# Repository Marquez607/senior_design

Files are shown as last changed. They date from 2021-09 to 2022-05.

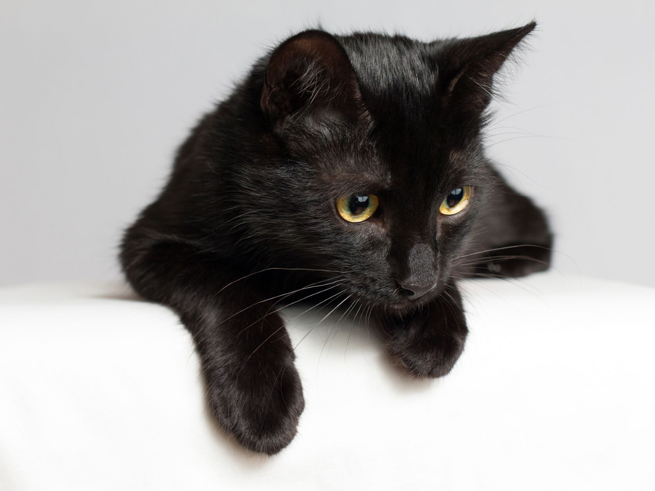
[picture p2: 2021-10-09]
Python/client_scripts/image_testing/test_cat.jpg

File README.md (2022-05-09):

# Wheelson IoT Drone Platform
Senior Design 2021 project by Marquez Jones and Daniel Olis \
Project consisted of making wifi connected robot platform that provided video streaming to end user on web application written with PyWebio. 

## MCU DETAILS 
### CC3235S <- base MCU 
* https://www.ti.com/product/CC3235S#design-development
### Launchpad :
* link: https://www.ti.com/tool/LAUNCHXL-CC3235S
### CC3235MODAS <- module that has antenna solution implemented
* link: https://www.ti.com/product/CC3235MODAS?keyMatch=&tisearch=search-everything&usecase=partmatches
### Launchpad :
* link: https://www.ti.com/tool/LAUNCHCC3235MOD

### NOTE: clean project before each build to make sure image file gets generated
* https://dev.ti.com/tirex/explore/node?node=AFiRjv8UYvIlGLFBWWEcQw__fc2e6sr__LATEST

### OUR BOARD
* may need to have a serial flash along side the MCU, steal the one from TI schematics
* Might only be necessary if we use the SysConfig ImageCreator 
* https://dev.ti.com/tirex/explore/node?node=AFiRjv8UYvIlGLFBWWEcQw__fc2e6sr__LATEST

<!-- ## Machine Learning 
Part of the project could be incorporating a camera to detect something. Right now it'd be 
cool if we could tell the drone to go to x,y gps location and look for trash. We can just 
get some trash dataset and train an support vector machine (or some other light weight ML model)

TinyML Guide (porting sklearn to c/++)
https://techcommunity.microsoft.com/t5/educator-developer-blog/using-tinyml-to-classify-audio/ba-p/2163436

Trash classification:
https://medium.com/geekculture/classifying-waste-images-with-machine-learning-14b249f11544#66db

Kaggle Waste Dataset:
https://www.kaggle.com/techsash/waste-classification-data -->

## WIFI CONNECTIVITY
For sanity's sake, the system will get deployed on using a LAN router we have control over
I'll be using a static IP address for the robot/drone that I'll configure using the router. 
Without a static IP, I'd probably have to seput some kind of website or blah blah blah 

## USER INTERFACE
We can quickly make a webapp using pywebio:
https://pywebio.readthedocs.io/en/latest/search.html?q=image&check_keywords=yes&area=default#

This can be hosted on the same "server" as the wifi drone controller which will just be a computer on our LAN network.
This way, it can be used on both PC and mobile without having to compile multiple applications and should be sufficient 
for the scope of this project. 

Jank way to implement video streaming in pywebio:
https://github.com/pywebio/PyWebIO/issues/107

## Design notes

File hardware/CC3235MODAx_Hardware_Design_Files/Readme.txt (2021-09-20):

CC3235MODAx Hardware Design Files v1.00.00
Texas Instruments, Inc.

********************************************************************************
Welcome to the CC3235MODAx Dual-Band Wi-Fi Wireless MCU Module!
********************************************************************************

In this package, you will find hardware design files that can help you quickly
get started on developing your own project.

Available in the 'Hardware' folder are the complete board schematic and layout,
bill of material and Gerber files. This board was designed using Altium.

You can also a web link in the 'Documentation' folder pointing to
the Product Page.

For more resources, be sure to visit www.ti.com/product/cc3235moda

********************************************************************************
Revision History
********************************************************************************
Ver 1.00.00 - October 2, 2019
- Initial Release of Rev A

********************************************************************************
Project File Listing
********************************************************************************
|--Documentation                      : Folder containing links to more resources
|--Hardware                           : Folder containing hardware design files,
                                        bill of material and gerber files
|--Readme.txt                         : This file

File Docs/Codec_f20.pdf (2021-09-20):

# GND Tip

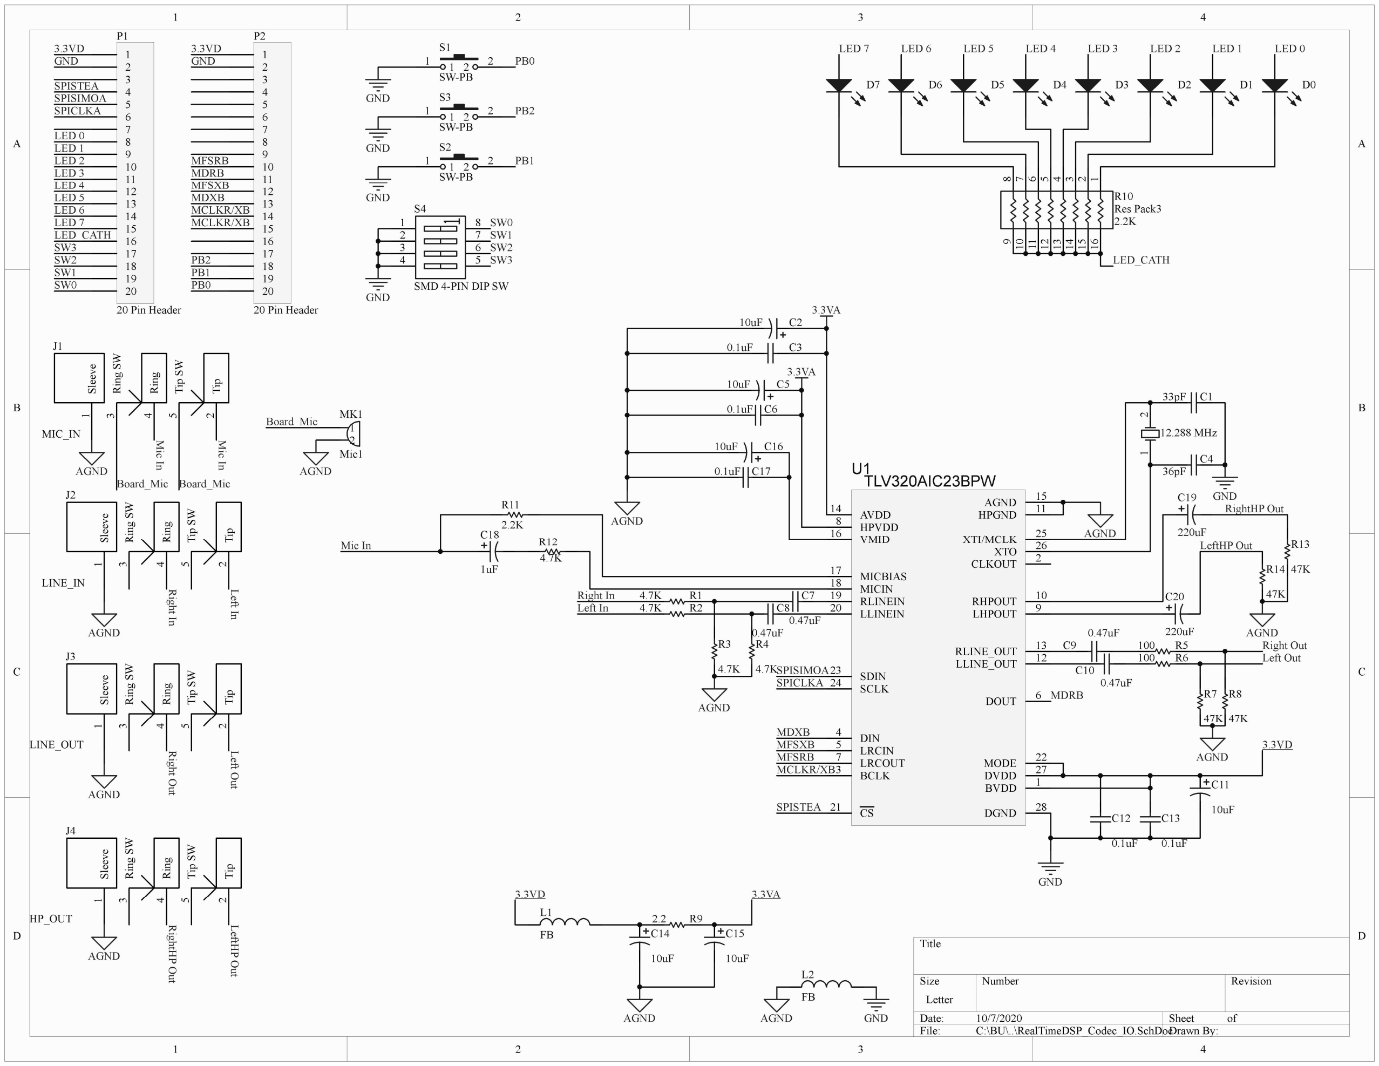
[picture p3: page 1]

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
Title

Size | Number | | Revision
Letter
Date: | 10/7/2020 | Sheet | of
File: | C:\BU\..\RealTimeDSP_Codec_IO.SchDocDrawn By:
0.1uF | C3
10uF | C2

0.1uF C6

10uF C5

AGND

0.47uF

C7

0.47uF

C8

4.7K | R1
4.7K | R2

4.7K

R4

4.7K

R3

Right In
Left In

AGND

33pF C1

36pF

C4 ¹ ² 12.288 MHz

GND

AGND

0.47uF

C10

0.47uF
C9

47K

R7

47K

R8

100 R5
100 R6

Right Out
Left Out

AGND

0.1uF

C12

0.1uF

C13

10uF

C11

GND

3.3VD

L1

FB

3.3VD

10uF

C14

10uF

C15

### 2.2 R9

3.3VA

AGND | AGND | GND

L2

FB Tip

### 2 Ring

### 4 Sleeve 1 Ring SW 3 Tip SW

5

J2

LINE_IN | Tip

### 2 Ring

### 4 Sleeve 1 Ring SW 3 Tip SW

5

J3

LINE_OUT

AGND | Right In | Left In
AGND | Right Out | Left Out

SPICLKA

MDXB
MFSXB
MFSRB

SPISTEA

MDRB

LHPOUT 9

LRCOUT 7

RHPOUT | 10
DOUT | 6
XTO | 26
RLINE_OUT | 13
LLINE_OUT | 12
CLKOUT | 2
MICBIAS 17
HPGND | 11
DGND | 28
AGND | 15

SDIN 23

DIN 4

CS 21

MODE 22

VMID 16

MICIN 18

LRCIN 5

XTI/MCLK 25

RLINEIN 19
LLINEIN 20

SCLK 24

HPVDD 8

DVDD | 27
BVDD | 1

AVDD 14

BCLK 3

U1

## TLV320AIC23BPW

SPISIMOA

MCLKR/XB

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
### 20 Pin Header

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
SMD 4-PIN DIP SW
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
### 20 Pin Header Tip

### 2 Ring

### 4 Sleeve 1 Ring SW 3 Tip SW

5

J1

MIC_IN

AGND

10uF C16

0.1uF C17

3.3VA

3.3VA Mic In | Mic In

2.2K

R11

Mic In
4.7K

R12

1

1
2

2

S1

SW-PB

1

1
2

2

S2

SW-PB

GND

PB2 1

1
2

2

S3

SW-PB

D7 | D6 | D5 | D4 | D3 | D2 | D1 | D0 8

7

6

5

4

3

2

1 101112131415169

2.2K

R10
Res Pack3
LED 7 | LED 6 | LED 5 | LED 4 | LED 3 | LED 2 | LED 1 | LED 0

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
220uF

C19

220uF

C20

47K

R13

47K

R14

AGND

LED_CATH

3.3VD

### 2 Ring

### 4 Sleeve 1 Ring SW 3 Tip SW

5

J4

HP_OUT

1
2

MK1

Mic1

Board_Mic

AGND

# Board_Mic Board_Mic RightHP Out LeftHP Out

RightHP Out

LeftHP Out

AGND

LED 0
LED 1
LED 2
LED 3
LED 4
LED 5
LED 6
LED 7

MFSRB
MDRB
MFSXB
MDXB
MCLKR/XB
MCLKR/XB

3.3VD
GND

LED_CATH

SPISTEA
SPISIMOA
SPICLKA

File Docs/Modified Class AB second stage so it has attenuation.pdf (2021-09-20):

Modified Class AB second stage so it has attenuation. You need to do this if your signal is on the level of 1V or more going into the Class AB power amplifier. You can tweak the values to get the Class AB response louder.

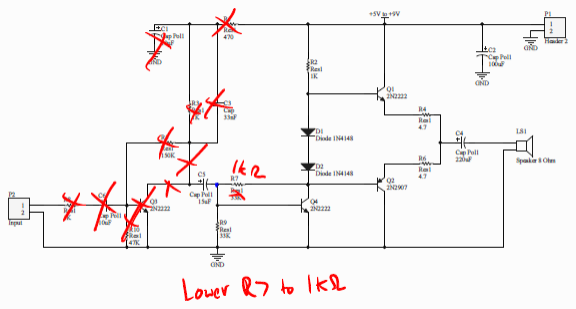
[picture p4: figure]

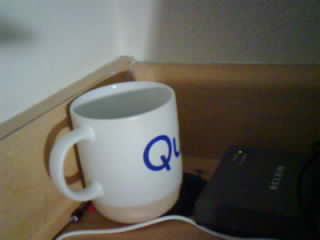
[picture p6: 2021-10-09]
Python/client_scripts/good_images/snap_5.jpg

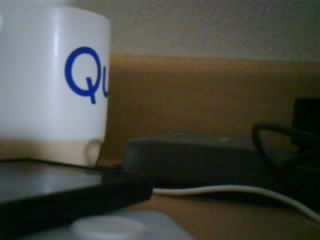
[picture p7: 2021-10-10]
Python/client_scripts/rx_images/snap_3.jpg

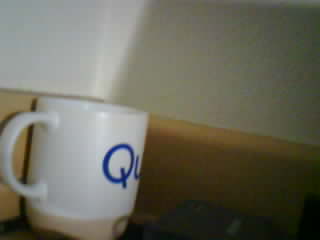
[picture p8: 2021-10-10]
Python/client_scripts/rx_images/snap_86.jpg

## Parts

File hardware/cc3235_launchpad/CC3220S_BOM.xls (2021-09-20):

Filename: | WCS002A_CC3220S_BOM.xls
Variant: | 002
Generated: | 12/6/2016 1:31:22 PM
 |  | CC3220S-LAUNCHXL
Designator | Quantity | Value | Description | PackageReference | PartNumber | Manufacturer | Alternate PartNumber | Alternate Manufacturer
!PCB1 | 1 |  | Printed Circuit Board |  | WCS002 | Any | - | -
C1, C4, C5, C14, C17, C24, C25, C28, C32, C33, C36, C37, C38, C43, C44, C46, C47, C57, C58, C59 | 20 | 0.1uF | CAP, CERM, 0.1 µF, 10 V, +/- 10%, X5R, 0402 | 0402 | C1005X5R1A104K050BA | TDK
C2, C3, C7, C8, C9, C15, C21, C53, C54, C55, C56 | 11 | 0.01uF | CAP, CERM, 0.01 µF, 16 V, +/- 10%, X7R, 0402 | 0402 | C1005X7R1C103K | TDK
C6, C13 | 2 | 22pF | CAP, CERM, 22 pF, 50 V, +/- 1%, C0G/NP0, 0402 | 0402 | GRM1555C1H220FA01D | MuRata
C10, C11, C19 | 3 | 0.1uF | CAP, CERM, 0.1 µF, 25 V, +/- 10%, X5R, 0603 | 0603 | 06033D104KAT2A | AVX
C12, C16, C20, C22, C23 | 5 | 1uF | CAP, CERM, 1 µF, 16 V, +/- 10%, X5R, 0402 | 0402 | C1005X5R1C105K050BC | TDK
C18 | 1 | 2.2uF | CAP, CERM, 2.2 µF, 16 V, +/- 10%, X5R, 0402 | 0402 | C1005X5R1C225K050BC | TDK
C26, C48, C49 | 3 | 10pF | CAP, CERM, 10 pF, 50 V, +/- 5%, C0G/NP0, 0402 | 0402 | GRM1555C1H100JA01D | MuRata
C27 | 1 | 1uF | CAP, CERM, 1 µF, 10 V, +/- 10%, X5R, 0402 | 0402 | GRM155R61A105KE15D | MuRata
C29, C30, C31 | 3 | 4.7uF | CAP, CERM, 4.7 µF, 6.3 V, +/- 20%, X5R, 0402 | 0402 | C1005X5R0J475M050BC | TDK
C34 | 1 | 0.5pF | CAP, CERM, 0.5 pF, 50 V, +/- 10%, C0G/NP0, 0402 | 0402 | GJM1555C1HR50BB01J | MuRata
C35, C42, C45 | 3 | 10uF | CAP, CERM, 10 µF, 6.3 V, +/- 20%, X5R, 0603 | 0603 | GRM188R60J106ME47D | MuRata
C39, C40 | 2 | 22uF | CAP, CERM, 22 µF, 4 V, +/- 20%, X5R, 0603 | 0603 | C1608X5R0G226M080AA | TDK
C41 | 1 | 1uF | CAP, CERM, 1 µF, 10 V, +/- 10%, X5R, 0402 | 0402 | C1005X5R1A105K050BB | TDK
C50, C51 | 2 | 6.2pF | CAP, CERM, 6.2 pF, 50 V, +/- 5%, C0G/NP0, 0402 | 0402 | GRM1555C1H6R2CA01D | MuRata
C52 | 1 | 0.01uF | CAP, CERM, 0.01 µF, 10 V, +/- 10%, X5R, 0402 | 0402 | GRM155R61A103KA01D | MuRata
C60, C62 | 2 | 10uF | CAP, CERM, 10 µF, 10 V, +/- 10%, X5R, 0805 | 0805 | GRM21BR61A106KE19L | MuRata
C61 | 1 | 22uF | CAP, CERM, 22 µF, 16 V, +/- 10%, X5R, 0805 | 0805 | C2012X5R1C226K125AC | TDK
C63, C64 | 2 | 100uF | CAP, CERM, 100 µF, 6.3 V, +/- 20%, X5R, 1206 | 1206 | GRM31CR60J107ME39L | MuRata
D1, D8 | 2 | Green | LED, Green, SMD | LED, GREEN, 0603 | SML-LX0603GW-TR | Lumex
D2, D6, D7, D10 | 4 | Red | LED, Red, SMD | LED, 1.6x.8x.8mm | SML-311UTT86 | Rohm
D3, D9 | 2 | Yellow | LED, Yellow, SMD | LED_0603 | 150060YS75000 | Wurth Elektronik eiSos
D4, D5 | 2 | 45V | Diode, Schottky, 45 V, 0.03 A, 0603 Diode | 0603 Diode | CD0603-B00340 | Bourns
E1 | 1 |  | ANT BLUETOOTH W-LAN ZIGBEE WIMAX, SMD | 3.2x1.6mm | AH316M245001-T | Taiyo Yuden
FL1 | 1 | 1.02 dB | Multilayer Chip Band Pass Filter For 2.4GHz W-LAN/Bluetooth, SMD | 2x1.25mm | DEA202450BT-1294C1-H | TDK
J1 | 1 |  | Connector, Receptacle, Micro-USB Type B, R/A, Bottom Mount SMT | Micro USB receptacle | 105017-0001 | Molex
J3 | 1 |  | Header, 2.54 mm, 5x2, Gold, TH | Header, 2.54mm, 5x2, TH | 61301021121 | Wurth Elektronik
J4, J8 | 2 |  | Header, 1.27 mm, 5x2, Gold, TH | Header, 1.27 mm, 5x2, TH | FTSH-105-01-F-D-K | Samtec
J5, J6, J22, J23 | 4 |  | Header, 2.54 mm, 3x1, Gold, TH | Header, 2.54mm, 3x1, TH | 61300311121 | Wurth Elektronik
J7 | 1 |  | Header, 1.27mm, 7x2, Gold, SMT | Header, 1.27mm, 7x2, SMT | FTSH-107-01-F-DV | Samtec
J9, J15, J16, J17, J18, J19, J20, J21, J24 | 9 |  | Header, 2.54 mm, 2x1, Gold, TH | Header, 2.54mm, 2x1, TH | 61300211121 | Wurth Elektronik
J10 | 1 |  | Connector, Ultra-Mini Coaxial, SMD | Ultra small CO-AX SMD | U.FL-R-SMT-1 | Hirose Electric Co. Ltd.
J11 | 1 |  | Coaxial Connectors with Switch, 50 Ohm, SMD | Coaxial Connector with Switch | MM8030-2610RJ3 | MuRata
J13 | 1 |  | Header, 2.54mm, 3x2, Gold, TH | Header, 2.54mm, 3x2, TH | 61300621121 | Wurth Elektronik
L1, L2 | 2 | 10 ohm | Ferrite Bead, 10 ohm @ 100 MHz, 1 A, 0402 | 0402 | BLM15AG100SN1D | MuRata
L3 | 1 | 3.3nH | Inductor, Multilayer, Air Core, 3.3 nH, 0.3 A, 0.17 ohm, SMD | 0402 polarized | LQG15HS3N3S02D | MuRata
L4, L6 | 2 | 2.2uH | Inductor, Multilayer, Ferrite, 2.2 µH, 1.3 A, 0.08 ohm, SMD | SMD, Body 2.5x2mm, Height 1.2mm | LQM2HPN2R2MG0L | MuRata
L5 | 1 | 1uH | Inductor, Multilayer, Ferrite, 1 µH, 1.6 A, 0.055 ohm, SMD | SMD, Body 2.5x2mm, Height 1.2mm | LQM2HPN1R0MG0L | MuRata
L8 | 1 | 2.2uH | Inductor, Wirewound, 2.2 µH, 1 A, 0.143 ohm, SMD | 0805_140 | BRC2012T2R2MD | Taiyo Yuden
LBL1 | 1 |  | Thermal Transfer Printable Labels, 0.650" W x 0.200" H - 10,000 per roll | PCB Label 0.650"H x 0.200"W | THT-14-423-10 | Brady | - | -
P1, P2, P3, P4 | 4 |  | Connector, Receptacle, 100mil, 10x1, Gold plated, TH | 10x1 Receptacle | SSW-110-23-F-S | Samtec
Q1, Q4, Q6, Q7 | 4 | 50V | MOSFET, N-CH, 50 V, 0.22 A, SOT-23 | SOT-23 | BSS138 | Fairchild Semiconductor |  | None
Q2 | 1 | -50V | MOSFET, P-CH, -50 V, -0.13 A, AEC-Q101, SOT-363 | SOT-363 | BSS84DW-7-F | Diodes Inc. |  | None
Q3, Q5 | 2 | -30V | MOSFET, P-CH, -30 V, -1.5 A, SSOT-3 | SSOT-3 | FDN358P | Fairchild Semiconductor |  | None
R1, R2, R3, R4, R5, R6, R8, R27, R31 | 9 | 33.0 | RES, 33.0, 1%, 0.1 W, 0402 | 0402 | ERJ-2RKF33R0X | Panasonic
R7, R9, R10, R11, R25, R29, R30, R32, R137, R138, R139, R144 | 12 | 1.0k | RES, 1.0 k, 5%, 0.063 W, 0402 | 0402 | CRCW04021K00JNED | Vishay-Dale
R12, R39, R40, R43, R44, R45, R46, R60, R62, R64, R67, R68, R70, R71, R72, R74, R75, R76, R78, R80, R81, R82, R83, R84, R85, R86, R87, R88, R89, R90, R91, R92, R116, R117, R121, R123, R126, R128, R129, R130, R132, R133, R134, R135, R154 | 45 | 0 | RES, 0, 5%, 0.063 W, 0402 | 0402 | ERJ-2GE0R00X | Panasonic
R13 | 1 | 100 | RES, 100, 5%, 0.063 W, 0402 | 0402 | CRCW0402100RJNED | Vishay-Dale
R14 | 1 | 100k | RES, 100 k, 5%, 0.1 W, 0603 | 0603 | CRCW0603100KJNEA | Vishay-Dale
R15 | 1 | 330k | RES, 330 k, 5%, 0.063 W, 0402 | 0402 | CRCW0402330KJNED | Vishay-Dale
R16 | 1 | 220k | RES, 220 k, 5%, 0.063 W, 0402 | 0402 | CRCW0402220KJNED | Vishay-Dale
R17, R26, R41, R48, R49, R50, R136, R146, R151, R152, R153 | 11 | 100k | RES, 100 k, 5%, 0.063 W, 0402 | 0402 | CRCW0402100KJNED | Vishay-Dale
R51 | 1 | 2.7k | RES, 2.7 k, 5%, 0.063 W, 0402 | 402 | CRCW04022K70JNED | Vishay-Dale
R18, R19 | 2 | 220 | RES, 220, 5%, 0.1 W, 0603 | 0603 | CRCW0603220RJNEA | Vishay-Dale
R20, R35, R53, R141, R142 | 5 | 10k | RES, 10 k, 5%, 0.063 W, 0402 | 0402 | CRCW040210K0JNED | Vishay-Dale
R21 | 1 | 100 | RES, 100, 1%, 0.1 W, 0402 | 0402 | ERJ-2RKF1000X | Panasonic
R22 | 1 | 100 | RES, 100, 1%, 0.063 W, 0402 | 0402 | CRCW0402100RFKED | Vishay-Dale
R23 | 1 | 4.87k | RES, 4.87 k, 1%, 0.1 W, 0603 | 0603 | CRCW06034K87FKEA | Vishay-Dale
R24, R143, R145, R147, R148, R149 | 6 | 270 | RES, 270, 5%, 0.1 W, 0603 | 0603 | CRCW0603270RJNEA | Vishay-Dale
R28 | 1 | 51 | RES, 51, 5%, 0.063 W, 0402 | 0402 | CRCW040251R0JNED | Vishay-Dale
R33, R34 | 2 | 33 | RES, 33, 5%, 0.1 W, 0603 | 0603 | CRCW060333R0JNEA | Vishay-Dale
R36, R57 | 2 | 0 | RES, 0, 5%, 0.1 W, 0603 | 0603 | ERJ-3GEY0R00V | Panasonic
R47 | 1 | 270 | RES, 270, 5%, 0.063 W, 0402 | 0402 | CRCW0402270RJNED | Vishay-Dale
R52 | 1 | 2.2k | RES, 2.2 k, 5%, 0.063 W, 0402 | 0402 | CRCW04022K20JNED | Vishay-Dale
R102, R105, R110, R111 | 4 | 470 | RES, 470, 1%, 0.1 W, 0402 | 0402 | ERJ-2RKF4700X | Panasonic
R103, R104, R112, R113 | 4 | 576k | RES, 576 k, 1%, 0.063 W, 0402 | 0402 | CRCW0402576KFKED | Vishay-Dale
R106, R107, R114, R115 | 4 | 422k | RES, 422 k, 1%, 0.063 W, 0402 | 0402 | CRCW0402422KFKED | Vishay-Dale
R118, R119 | 2 | 3.3k | RES, 3.3 k, 5%, 0.063 W, 0402 | 0402 | CRCW04023K30JNED | Vishay-Dale
R140 | 1 | 100k | RES, 100 k, 1%, 0.1 W, 0402 | 0402 | ERJ-2RKF1003X | Panasonic
SW1, SW2, SW3 | 3 |  | Switch, SPST-NO, Off-Mom, 1 Pos, 0.05A, 12VDC, TH | 7.3x5.9mm | MJTP1117 | APEM
SW4 | 1 |  | Switch, Tactile, SPST-NO, SMT | Switch, 6.1x1.8x4.6 mm | EVQ-PSD02K | Panasonic
TP2 | 1 | SMT | Test Point, Miniature, SMT | Testpoint_Keystone_Miniature | 5015 | Keystone
U1 | 1 |  | Tiva C Series Microcontroller, PDT0128A | PDT0128A | TM4C1294NCPDTI3R | Texas Instruments | TM4C1294NCPDTI3 | Texas Instruments
U2 | 1 |  | ESD Solution for High-Speed Differential Interface, 4 Channels, -40 to +85 degC,10-pin SON (DQA), Green (RoHS & no Sb/Br) | DQA0010A | TPD4S010DQAR | Texas Instruments | Equivalent | Texas Instruments
U3, U4, U6 | 3 |  | Single-Bit Dual-Supply Bus Transceiver With Configurable Voltage Translation and 3-State Outputs, DCK0006A | DCK0006A | SN74LVC1T45DCKR | Texas Instruments | SN74LVC1T45DCKT | Texas Instruments
U5 | 1 |  | Precision Micropower Shunt Voltage Reference, 0.2% accuracy, 2.5 V, 15 ppm / degC, 15 mA, -40 to 85 degC, 3-pin SOT-23 (DBZ), Green (RoHS & no Sb/Br) | DBZ0003A | LM4040B25IDBZR | Texas Instruments | Equivalent | Texas Instruments
U7 | 1 |  | SimpleLink Wi-Fi and Internet-of-Things Solution, a Single-Chip Wireless MCU, RGK0064B (VQFN-64) | RGK0064B | CC3220SM2ARGKR | Texas Instruments | CC3220SM2ARGKT | Texas Instruments
U8 | 1 |  | ULTRA LOW POWER, 32M-BIT [x 1/x 2/x 4] CMOS MXSMIO(SERIAL MULTI I/O) FLASH MEMORY, SOP-8 | 8-SOP | MX25R3235FM1IL0 | Macronix International Co., LTD
U9 | 1 |  | Low Cost, Low Power, Rail-to-Rail Operational Amplifier MicroAmplifier(TM) Series, 2.7 to 5.5 V, -55 to 125 degC, 14-pin SOP (PW0014A), Green (RoHS & no Sb/Br) | PW0014A | OPA4342EA/250 | Texas Instruments | Equivalent | None
U10 | 1 |  | Infrared Thermopile Sensor in Chip-Scale Package, YZF0008AEAE | YZF0008AEAE | TMP006AIYZF | Texas Instruments |  | Texas Instruments
U11 | 1 |  | Digital, triaxial acceleration sensor, 12LGA | LGA, 12-Leads, Body 2x2mm, Pitch 0.5mm | BMA222E | Bosch Solar Energy
U12 | 1 |  | Buck Step Down Regulator with 3 to 17 V Input and 3.3 V Output, -40 to 85 degC, 8-Pin WSON (DSG), Green (RoHS & no Sb/Br) | DSG0008A | TPS62162DSGR | Texas Instruments | Equivalent | Texas Instruments
Y1 | 1 |  | Crystal, 16 MHz, 18 pF, SMD | ABM3 | ABM3-16.000MHZ-D2Y-T | Abracon Corportation
Y2 | 1 |  | CRYSTAL, 32.768KHZ, 9PF, SMD | 3.2x0.9x1.5mm | ABS07-32.768KHZ-9-T | Abracon Corportation
Y3 | 1 |  | Crystal, 40MHz, 8pF, SMD | 2.5x2mm | Q24FA20H0039600 | Epson
FID1, FID2, FID3, FID4, FID5, FID6 | 0 |  | Fiducial mark. There is nothing to buy or mount. | Fiducial | N/A | N/A
J14 | 0 |  | Header, 2.54 mm, 2x1, Gold, TH | Header, 2.54mm, 2x1, TH | 61300211121 | Wurth Elektronik
L7 | 0 | 10uH | Inductor, Wirewound, Ceramic, 10 µH, 0.48 A, 0.36 ohm, SMD | 2.5x1.8x1.8mm | CBC2518T100M | Taiyo Yuden
R37, R38, R42, R54, R55, R58, R59, R61, R63, R65, R66, R69, R73, R77, R79, R93, R94, R95, R96, R97, R98, R99, R100, R101, R108, R109, R120, R122, R124, R127, R131 | 0 | 0 | RES, 0, 5%, 0.063 W, 0402 | 0402 | ERJ-2GE0R00X | Panasonic
R56, R150 | 0 | 0 | RES, 0, 5%, 0.1 W, 0603 | 0603 | ERJ-3GEY0R00V | Panasonic
R125 | 0 | 0 | RES, 0, 5%, 0.125 W, 0805 | 0805 | ERJ-6GEY0R00V | Panasonic
 |  | Notes:
 |  | Unless otherwise noted in the Alternate PartNumber and/or Alternate Manufacturer columns, all parts may be substituted with equivalents.

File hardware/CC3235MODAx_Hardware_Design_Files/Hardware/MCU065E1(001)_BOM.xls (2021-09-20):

Filename: | #VALUE!
Variant: | 001
Generated: | 10/2/2019 2:32:45 PM
 |  | LAUNCHCC3235MODAS
Designator | Quantity | Value | Description | PackageReference | PartNumber | Manufacturer | Alternate PartNumber | Alternate Manufacturer
!PCB1 | 1 |  | Printed Circuit Board |  | MCU065 | Any
C1 | 1 | 0.1uF | CAP, CERM, 0.1 uF, 10 V,+/- 10%, X5R, 0402 | 0402 | LMK105BJ104KV-F | Taiyo Yuden
C2, C5, C6, C7, C12, C14 | 6 | 0.01uF | CAP, CERM, 0.01 µF, 16 V,+/- 10%, X7R, 0402 | 0402 | CL05B103KO5NNNC | Samsung Electro-Mechanics
C3, C13, C15, C18 | 4 | 1uF | CAP, CERM, 1 uF, 16 V, +/- 10%, X5R, 0402 | 0402 | EMK105BJ105KVHF | Taiyo Yuden
C4, C11 | 2 | 22pF | CAP, CERM, 22 pF, 50 V,+/- 5%, C0G/NP0, 0402 | 0402 | CL05C220JB5NNNC | Walsin
C8, C9, C10, C17 | 4 | 0.1uF | CAP, CERM, 0.1 uF, 25 V, +/- 10%, X5R, 0603 | 0603 | 06033D104KAT2A | AVX
C16 | 1 | 2.2uF | CAP, CERM, 2.2 uF, 16 V, +/- 10%, X5R, 0402 | 0402 | C1005X5R1C225K050BC | TDK
C19, C20, C22, C23, C29, C30, C31, C32, C33, C34, C40, C41, C42 | 13 | 0.1uF | CAP, CERM, 0.1 uF, 10 V, +/- 10%, X5R, 0402 | 0402 | GRM155R61A104KA01D | MuRata
C21, C36, C37, C38, C39 | 5 | 0.01uF | CAP, CERM, 0.01 uF, 16 V, +/- 10%, X7R, 0402 | 0402 | GRM155R71C103KA01D | MuRata
C24, C26 | 2 | 10uF | CAP, CERM, 10 uF, 10 V, +/- 10%, X5R, 0805 | 0805 | GRM21BR61A106KE19L | MuRata | CL21A106KPFNNNE | SAMSUNG
C25 | 1 | 22uF | CAP, CERM, 22 uF, 16 V, +/- 10%, X5R, 0805 | 0805 | C2012X5R1C226K125AC | TDK | ---- | ----
C27, C28 | 2 | 100uF | CAP, CERM, 100 uF, 6.3 V, +/- 20%, X5R, 1206 | 1206 | GRM31CR60J107ME39L | MuRata | CL31A107MQHNNNE | SAMSUNG
C35 | 1 | 0.01uF | CAP, CERM, 0.01 uF, 10 V, +/- 10%, X5R, 0402 | 0402 | GRM155R61A103KA01D | MuRata
CC1 | 1 |  | SimpleLink Wi-Fi and Internet-of-Things Module Solution, a Single-Chip Wireless MCU, MOB0063A (SIP MODULE-63) | MON0063A | CC3235MODASM2MONR | Texas Instruments |  | Texas Instruments
D1 | 1 | Green | LED, Green, SMD | LED, GREEN, 0603 | SML-LX0603GW-TR | Lumex
D2 | 1 | Red | LED, Red, SMD | SMD, 2-Leads, Body 1.6x0.8mm | 19-217/R6C-AL1M2VY/3T | Everlight
D3 | 1 | Yellow | LED, Yellow, SMD | LED_0603 | 150060YS75000 | Wurth Elektronik | 19-217/G7C-AN1P2/3T | Everlight
D4, D8 | 2 | Red | LED, Red, SMD | LED, 1.6x.8x.8mm | SML-311UTT86 | Rohm | 19-217/R6C-AL1M2VY/3T | Everlight
D5, D6 | 2 | 45V | Diode, Schottky, 45 V, 0.03 A, SOD-523F | SOD-523F | CDBU00340 | Comchip Technology
D7 | 1 | RGB | LED, RGB, TH | 1.6x1.6mm | 19-337/R6GHBHC-A01/2T | Everlight
H1, H2, H3, H4 | 4 |  | Spacer Support, Nylon 66 | Spacer Nylon Support | MAE-10 | Kang Yang
J1 | 1 |  | Receptacle, USB 2.0, Micro B, 5 Position, R/A, SMT | Receptacle, USB 2.0, Micro B, 5 Pos, 0.65mm Pitch, R/A, SMT | 1051640001 | Molex
J2, J6 | 2 |  | Header, 1.27 mm, 5x2, Gold, TH | Header, 1.27 mm, 5x2, TH | FTSH-105-01-F-D-K | Samtec | ---- | ----
J3 | 1 |  | Header, 1.27mm, 7x2, Gold, SMT | Header, 1.27mm, 7x2, SMT | FTSH-107-01-F-DV | Samtec | ---- | ----
J5 | 1 |  | Header, 2.54 mm, 5x2, Gold, TH | Header, 2.54mm, 5x2, TH | 61301021121 | Wurth Elektronik
J7, J8, J9, J10, J21, J22, J23, J24, J25 | 9 |  | Header, 2.54 mm, 2x1, Gold, TH | Header, 2.54mm, 2x1, TH | 61300211121 | Wurth Elektronik
J11, J12, J16 | 3 |  | Header, 2.54 mm, 3x1, Gold, TH | Header, 2.54mm, 3x1, TH | 61300311121 | Wurth Elektronik
J13 | 1 |  | Header, 2.54mm, 2x1, TH | Header, 2.54mm, 2x1, TH | 961102-6404-AR | 3M
J18 | 1 |  | Header, 2.54mm, 3x2, Gold, TH | Header, 2.54mm, 3x2, TH | 61300621121 | Wurth Elektronik
J19, J20 | 2 |  | Header, 100mil, 3x1, Tin, TH | Header, 3 PIN, 100mil, Tin | PEC03SAAN | Sullins Connector Solutions
L1, L2 | 2 | 10 ohm | Ferrite Bead, 10 ohm @ 100 MHz, 1 A, 0402 | 0402 | BLM15AG100SN1D | MuRata
L3 | 1 | 2.2uH | Inductor, Wirewound, 2.2 uH, 1 A, 0.143 ohm, SMD | 0805 | BRC2012T2R2MD | Taiyo Yuden | ---- | ----
LBL1 | 1 |  |  | PCB Label 0.650 x 0.200 inch | THT-14-423-10 | Brady
P1, P2 | 2 |  | Receptacle, 2.54mm, 10x2, Tin, TH | 10x2 Receptacle | SSQ-110-03-T-D | Samtec | CRD-081413-A-G | Major League Electronics
Q1, Q5, Q6, Q7 | 4 | 50V | MOSFET, N-CH, 50 V, 0.22 A, SOT-23 | SOT-23 | BSS138 | Fairchild Semiconductor |  | None
Q3 | 1 | -50V | MOSFET, 2-CH, P-CH, -50 V, -0.13 A, AEC-Q101, SOT-363 | SOT-363 | BSS84DW-7-F | Diodes Inc. |  | None
Q4 | 1 | -30V | MOSFET, P-CH, -30 V, -1.5 A, SSOT-3 | SSOT-3 | FDN358P | Fairchild Semiconductor |  | None
R1, R13, R16, R17, R18, R19, R20, R26, R148, R149, R154 | 11 | 1.0k | RES, 1.0 k, 5%, 0.063 W, AEC-Q200 Grade 0, 0402 | 0402 | CRCW04021K00JNED | Vishay-Dale
R2, R4, R6, R7, R8, R9, R10, R34, R37 | 9 | 33.0 | RES, 33.0, 1%, 0.1 W, 0402 | 0402 | ERJ-2RKF33R0X | Panasonic
R3, R45, R46, R104, R124, R125, R128, R130, R131, R135, R136, R137, R138, R140, R141 | 15 | 0 | RES, 0, 5%, 0.1 W, AEC-Q200 Grade 0, 0402 | 0402 | ERJ-2GE0R00X | Panasonic
R5 | 1 | 100 | RES, 100, 5%, 0.063 W, AEC-Q200 Grade 0, 0402 | 0402 | CRCW0402100RJNED | Vishay-Dale
R11 | 1 | 330k | RES, 330 k, 5%, 0.063 W, AEC-Q200 Grade 0, 0402 | 0402 | CRCW0402330KJNED | Vishay-Dale
R12 | 1 | 220k | RES, 220 k, 5%, 0.063 W, AEC-Q200 Grade 0, 0402 | 0402 | CRCW0402220KJNED | Vishay-Dale
R14, R15 | 2 | 220 | RES, 220, 5%, 0.1 W, AEC-Q200 Grade 0, 0603 | 0603 | CRCW0603220RJNEA | Vishay-Dale
R21, R22 | 2 | 33 | RES, 33, 5%, 0.1 W, AEC-Q200 Grade 0, 0603 | 0603 | CRCW060333R0JNEA | Vishay-Dale | RC0603JR-0733RL | YAGEO
R23 | 1 | 51 | RES, 51, 5%, 0.063 W, AEC-Q200 Grade 0, 0402 | 0402 | CRCW040251R0JNED | Vishay-Dale
R24, R29, R49, R52, R143, R155, R156 | 7 | 10k | RES, 10 k, 5%, 0.063 W, AEC-Q200 Grade 0, 0402 | 0402 | CRCW040210K0JNED | Vishay-Dale
R25 | 1 | 100 | RES, 100, 1%, 0.063 W, AEC-Q200 Grade 0, 0402 | 0402 | CRCW0402100RFKED | Vishay-Dale
R27 | 1 | 4.87k | RES, 4.87 k, 1%, 0.1 W, AEC-Q200 Grade 0, 0603 | 0603 | CRCW06034K87FKEA | Vishay-Dale
R28, R33, R36, R55, R56, R142, R150, R151, R152 | 9 | 100k | RES, 100 k, 5%, 0.063 W, AEC-Q200 Grade 0, 0402 | 0402 | CRCW0402100KJNED | Vishay-Dale
R30, R35, R153 | 3 | 270 | RES, 270, 5%, 0.1 W, AEC-Q200 Grade 0, 0603 | 0603 | CRCW0603270RJNEA | Vishay-Dale
R31 | 1 | 100k | RES, 100 k, 5%, 0.1 W, 0603 | 0603 | CRCW0603100KJNEAC | Vishay-Dale
R32 | 1 | 100 | RES, 100, 1%, 0.1 W, 0402 | 0402 | ERJ-2RKF1000X | Panasonic | RC0402FR-07100RL | YAGEO
R44 | 1 | 100k | RES, 100 k, 0.5%, 0.063 W, AEC-Q200 Grade 0, 0402 | 0402 | CRCW0402100KDHEDP | Vishay-Dale
R51 | 1 | 2.2k | RES, 2.2 k, 5%, 0.063 W, AEC-Q200 Grade 0, 0402 | 0402 | CRCW04022K20JNED | Vishay-Dale
R53, R54, R63, R64, R65, R67, R68, R69, R71, R72, R75, R77, R78, R79, R81, R82, R83, R85, R86, R87, R88, R89, R90, R91, R92, R93, R118, R121 | 28 | 0 | RES, 0, 5%, 0.063 W, 0402 | 0402 | RC0402JR-070RL | Yageo America
R57 | 1 | 0 | RES, 0, 5%, 0.1 W, 0603 | 0603 | ERJ-3GEY0R00V | Panasonic | RC0603FR-070RL | YAGEO
R108, R110, R116, R119 | 4 | 576k | RES, 576 k, 1%, 0.063 W, AEC-Q200 Grade 0, 0402 | 0402 | CRCW0402576KFKED | Vishay-Dale
R109, R111, R117, R120 | 4 | 470 | RES, 470, 1%, 0.1 W, AEC-Q200 Grade 0, 0402 | 0402 | ERJ-2RKF4700X | Panasonic
R112, R113, R122, R123 | 4 | 422k | RES, 422 k, 1%, 0.063 W, AEC-Q200 Grade 0, 0402 | 0402 | CRCW0402422KFKED | Vishay-Dale
R126, R127 | 2 | 3.3k | RES, 3.3 k, 5%, 0.063 W, AEC-Q200 Grade 0, 0402 | 0402 | CRCW04023K30JNED | Vishay-Dale
R144 | 1 | 100k | RES, 100 k, 1%, 0.1 W, 0402 | 0402 | ERJ-2RKF1003X | Panasonic
R145 | 1 | 261 | RES, 261, 1%, 0.063 W, AEC-Q200 Grade 0, 0402 | 0402 | CRCW0402261RFKED | Vishay-Dale
R146 | 1 | 309 | RES, 309, 1%, 0.063 W, AEC-Q200 Grade 0, 0402 | 0402 | CRCW0402309RFKED | Vishay-Dale
R147 | 1 | 200 | RES, 200, 5%, 0.063 W, AEC-Q200 Grade 0, 0402 | 0402 | CRCW0402200RJNED | Vishay-Dale
SH-J5-1, SH-J5-2, SH-J5-3, SH-J5-4, SH-J5-5, SH-J7, SH-J8, SH-J9, SH-J10, SH-J11, SH-J12, SH-J13, SH-J16, SH-J18, SH-J21, SH-J23, SH-J24, SH-J25 | 18 | 1x2 | Shunt, 100mil, Gold plated, Black | Shunt | SNT-100-BK-G | Samtec | 969102-0000-DA | 3M
SW1, SW2, SW3 | 3 |  | Switch, SPST-NO, 1 Pos, 0.05A, 12VDC, SMD | 7.8x3.5mm | TL3330AF260QG | E-Switch
SW4 | 1 |  | Switch, SPST-NO, Off-Mom, 0.05 A, 12 VDC, SMT | 3x2.5mm | B3U-3000P | Omron Electronic Components
TP2 | 1 |  | Test Point, Miniature, SMT | Testpoint_Keystone_Miniature | 5015 | Keystone
U1 | 1 |  | MSP432E401YTPDT, PDT0128A (TQFP-128) | PDT0128A | MSP432E401YTPDT | Texas Instruments | MSP432E401YTPDTR | Texas Instruments
U2 | 1 |  | Precision Micropower Shunt Voltage Reference, 0.2% accuracy, 2.5 V, 15 ppm / degC, 15 mA, -40 to 85 degC, 3-pin SOT-23 (DBZ), Green (RoHS & no Sb/Br) | DBZ0003A | LM4040B25IDBZR | Texas Instruments
U3, U5, U7 | 3 |  | Single-Bit Dual-Supply Bus Transceiver with Configurable Voltage Translation and 3-State Outputs, DCK0006A, LARGE T&R | DCK0006A | SN74LVC1T45DCKR | Texas Instruments | SN74LVC1T45DCKT | Texas Instruments
U4 | 1 |  | ESD Solution for High-Speed Differential Interface, 4 Channels, -40 to +85 degC,10-pin SON (DQA), Green (RoHS & no Sb/Br) | DQA0010A | TPD4S010DQAR | Texas Instruments
U6 | 1 |  | Buck Step Down Regulator with 3 to 17 V Input and 3.3 V Output, -40 to 85 degC, 8-Pin WSON (DSG), Green (RoHS & no Sb/Br) | DSG0008A | TPS62162DSGR | Texas Instruments
U8 | 1 |  | 14 Bit, Digital, Triaxial Acceleration Sensor with Intelligent On-Chip Motion-Triggered Interrupt Controller, 12LGA | LGA, 12-Leads, Body 2x2mm, Pitch 0.5mm | BMA280 | Bosch Solar Energy
U10 | 1 |  | Low Cost, Low Power, Rail-to-Rail Operational Amplifier MicroAmplifier(TM) Series, 2.7 to 5.5 V, -55 to 125 degC, 14-pin SOP (PW14), Green (RoHS & no Sb/Br) | PW0014A | OPA4342EA/250 | Texas Instruments
U11 | 1 |  | High-Accuracy, Low-Power, Digital Temperature Sensor with SMBus and Two-Wire Serial Interface, DRV0006A (WSON-6) | DRV0006A | TMP116AIDRVR | Texas Instruments | TMP116AIDRVT | Texas Instruments
Y1 | 1 |  | Crystal, 16 MHz, 18 pF, SMD | ABM3 | ABM3-16.000MHZ-D2Y-T | Abracon Corporation | ---- | ----
J26, J27, J28 | 0 |  | Header, 2.54 mm, 2x1, Gold, TH | Header, 2.54mm, 2x1, TH | 61300211121 | Wurth Elektronik
Q2 | 0 | -30V | MOSFET, P-CH, -30 V, -1.5 A, SSOT-3 | SSOT-3 | FDN358P | Fairchild Semiconductor |  | None
R38, R39, R40, R41, R42, R43, R105, R129, R132, R133, R134, R139 | 0 | 0 | RES, 0, 5%, 0.1 W, AEC-Q200 Grade 0, 0402 | 0402 | ERJ-2GE0R00X | Panasonic
R47 | 0 | 100k | RES, 100 k, 5%, 0.063 W, AEC-Q200 Grade 0, 0402 | 0402 | CRCW0402100KJNED | Vishay-Dale
R58 | 0 | 0 | RES, 0, 5%, 0.1 W, 0603 | 0603 | ERJ-3GEY0R00V | Panasonic | RC0603FR-070RL | YAGEO
R59, R60, R61, R62, R66, R70, R73, R74, R76, R80, R84, R94, R95, R96, R97, R98, R99, R100, R101, R102, R103, R106, R107, R114, R115 | 0 | 0 | RES, 0, 5%, 0.063 W, 0402 | 0402 | RC0402JR-070RL | Yageo America
U9 | 0 |  | ULTRA LOW POWER, 64M-BIT [x 1/x 2/x 4] CMOS MXSMIO (SERIAL MULTI I/O) FLASH MEMORY, SOP-8 | SOP-8 | MX25R6435FM2IL0 | Macronix International Co., LTD
 |  | Notes:
 |  | Unless otherwise noted in the Alternate PartNumber and/or Alternate Manufacturer columns, all parts may be substituted with equivalents.

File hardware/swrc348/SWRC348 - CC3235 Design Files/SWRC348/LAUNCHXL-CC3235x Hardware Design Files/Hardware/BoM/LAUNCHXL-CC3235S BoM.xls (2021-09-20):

Filename: | #VALUE!
Variant: | 001
Generated: | 12/18/2018 3:03:33 PM
 |  | LAUNCHXL-CC3235S
Designator | Quantity | Value | Description | PackageReference | PartNumber | Manufacturer | Alternate PartNumber | Alternate Manufacturer
C2 | 1 | 8.2pF | CAP, CERM, 8.2 pF, 50 V,+/- 3%, C0G/NP0, 0402 | 0402 | 0402N8R2C500CT | Walsin | GRM1555C1H8R2CA01D | MuRata
C6 | 1 | 1.6pF | CAP, CERM, 1.6 pF, 50 V,+/- 7%, C0G/NP0, 0201 | 0201 | GRM0335C1H1R6BA01D | MuRata
C7 | 1 | 1.9pF | CAP, CERM, 1.9 pF, 50 V,+/- 2.6%, C0G/NP0, 0402 | 0402 | GJM1555C1H1R9WB01D | MuRata | GRM1555C1H1R9WA01D | MuRata
C8 | 1 | 2.2pF | CAP, CERM, 2.2 pF, 50 V,+/- 4.5%, C0G/NP0, 0402 | 0402 | GJM1555C1H2R2BB01D | MuRata | GRM1555C1H2R2BA01D | MuRata
C9, C10 | 2 | 4.7pF | CAP, CERM, 4.7 pF, 50 V,+/- 3%, C0G/NP0, 0201 | 0201 | GRM0335C1H4R7BA01D | MuRata
C14, C15 | 2 | 100pF | CAP, CERM, 100 pF, 25 V,+/- 5%, C0G/NP0, 0201 | 0201 | CC0201JRNPO8BN101 | Yageo | C0603C0G1E101J030BA
C17, C18, C19, C26, C28, C40, C41, C47, C48, C50, C52, C60, C61, C63, C75, C76, C77 | 17 | 0.1uF | CAP, CERM, 0.1 µF, 16 V,+/- 10%, X7R, 0402 | 0402 | CL05B104KO5NNNC | Walsin | C1005X5R1A104K050BA
C20, C22, C24, C29, C30, C31, C35, C49, C70, C71, C72, C73, C74 | 13 | 0.01uF | CAP, CERM, 0.01 µF, 50 V,+/- 10%, X7R, 0402 | 0402 | 0402B103K500CT | Walsin | C1005X7R1C103K050BA, GRM155R71E103KA01D, GRM155R61A103KA01D
C21, C23 | 2 | 22pF | CAP, CERM, 22 pF, 50 V,+/- 5%, C0G/NP0, 0402 | 0402 | CL05C220JB5NNNC | Walsin | GRM1555C1H220FA01D
C25, C27, C34, C36, C39 | 5 | 1uF | CAP, CERM, 1 µF, 25 V,+/- 10%, X5R, 0402 | 0402 | CL05A105KA5NQNC | Samsung Electro-Mechanics | C1005X5R1E105K050BC
C32, C33, C38 | 3 | 0.1uF | CAP, CERM, 0.1 uF, 25 V, +/- 10%, X5R, 0603 | 0603 | 06033D104KAT2A | AVX | 0603B104K250CT | Walsin
C37 | 1 | 2.2uF | CAP, CERM, 2.2 uF, 16 V, +/- 10%, X5R, 0402 | 0402 | C1005X5R1C225K050BC | TDK | CL05A225KA5NUNC | SAMSUNG
C42, C43, C45 | 3 | 4.7uF | CAP, CERM, 4.7 uF, 6.3 V,+/- 20%, X6S, 0402 | 0402 | JMK105BC6475MV-F | Taiyo Yuden | CL05A475MQ5NRNC | SAMSUNG
C44, C55, C68 | 3 | 0.6pF | CAP, CERM, 0.6pF, 25 V,+/- 16%, C0G/NP0, 0201 | 0201 | GJM0335C1ER60BB01D | MuRata
C46 | 1 | 0.5pF | CAP, CERM, 0.5 pF, 25 V,+/- 20%, C0G/NP0, 0201 | 0201 | GJM0335C1ER50BB01D | MuRata
C51, C59, C62 | 3 | 10uF | CAP, CERM, 10 uF, 10 V,+/- 20%, X6S, 0603 | 0603 | LMK107BC6106MA-T | Taiyo Yuden | CL10A106MP8NNNC | SAMSUNG
C53 | 1 | 0.2pF | CAP, CERM, 0.2pF, 25 V,+/- 50%, C0G/NP0, 0201 | 0201 | GJM0335C1ER20BB01D | MuRata
C54, C64 | 2 | 0.1uF | CAP, CERM, 0.1 uF, 10 V, +/- 10%, X5R, 0201 | 0201 | CL03A104KP3NNNC | Samsung Electro-Mechanics
C56, C57 | 2 | 22uF | CAP, CERM, 22 uF, 4 V,+/- 20%, X6S, 0603 | 0603 | GRM188C80G226ME15J | MuRata | CL10A226MQ8NRNC | SAMSUNG
C58 | 1 | 1uF | CAP, CERM, 1 µF, 10 V,+/- 20%, X5R, 0402 | 0402 | CL05A105MP5NNNC | Walsin | GRM155C81A105KA12D
C65, C66 | 2 | 10pF | CAP, CERM, 10 pF, 50 V,+/- 5%, C0G/NP0, 0402 | 0402 | 0402N100J500CT | Walsin | GRM1555C1H100JA01D
C67, C69 | 2 | 6.2pF | CAP, CERM, 6.2 pF, 50 V,+/- 4%, C0G/NP0, 0402 | 0402 | 0402N6R2C500CT | Walsin | GRM1555C1H6R2CA01D
C78, C80 | 2 | 10uF | CAP, CERM, 10 µF, 10 V,+/- 10%, X5R, 0805 | 0805 | CL21A106KPFNNNE | Samsung Electro-Mechanics | GRM21BR61A106KE19L
C79 | 1 | 22uF | CAP, CERM, 22 µF, 16 V,+/- 10%, X5R, 0805 | 0805 | CL21A226KOQNNNE | Samsung Electro-Mechanics | C2012X5R1C226K125AC
C81, C82 | 2 | 100uF | CAP, CERM, 100 uF, 6.3 V, +/- 20%, X5R, 1206 | 1206 | GRM31CR60J107ME39L | MuRata | CL31A107MQHNNNE | SAMSUNG
D1, D6, D8 | 3 | Red | LED, Red, SMD | LED, 1.6x.8x.8mm | 19-217/R6C-AL1M2VY/3T | Everlight | SML-311UTT86 | Rohm
D2 | 1 | Green | LED, Green, SMD | LED, GREEN, 0603 | SML-LX0603GW-TR | Lumex | 19-217/G7C-AN1P2/3T | Everlight
D3 | 1 | Yellow | LED, Yellow, SMD | LED_0603 | 150060YS75000 | Wurth Elektronik | 19-217/G7C-AN1P2/3T | Everlight
D4, D5 | 2 | 45V | Diode, Schottky, 45 V, 0.03 A, SOD-523F | SOD-523F | CDBU00340 | Comchip Technology | CD0603-B00340
D7 | 1 | Rgb | LED, Rgb, SMD | 1.6x1.6mm | EAST1616RGBA8 | Everlight | 19-337-R6GHBHC-C02-2T | Everlight
E1 | 1 |  | WLAN ANTENNA 802.11, SMD | 8x3mm | M830520 | Ethertronics | ---- | ----
FL1 | 1 | 1.02 dB | Multilayer Chip Band Pass Filter For 2.4GHz W-LAN/Bluetooth, SMD | 2x1.25mm | DEA202450BT-1294C1-H | TDK | ---- | ----
FL2 | 1 |  | Multilayer Band Pass Filter For 5GHz W-LAN/LTE-U | 1.6x0.8mm | DEA165538BT-2236B1-H | TDK | ---- | ----
H1 | 1 |  | Cable, USB-A to micro USB-B, 0.3 m |  | AK67421-0.3-VM | Assman WSW | GLJ-C4-1306 | ----
J2, J3 | 2 |  | Receptacle, Ultra Miniature Coaxial, Male Pin, 50 ohm, SMT | Ultra small CO-AX SMD | U.FL-R-SMT-1(01) | Hirose Electric Co. Ltd. | ---- | ----
J4 | 1 |  | Header, 2.54 mm, 5x2, Gold, TH | Header, 2.54mm, 5x2, TH | 61301021121 | Wurth Elektronik | ---- | ----
J6 | 1 |  | Receptacle, USB 2.0, Micro B, 5 Position, R/A, SMT | Receptacle, USB 2.0, Micro B, 5 Pos, 0.65mm Pitch, R/A, SMT | 1051640001 | Molex | ---- | ----
J7, J8 | 2 |  | Header, 1.27 mm, 5x2, Gold, TH | Header, 1.27 mm, 5x2, TH | FTSH-105-01-F-D-K | Samtec | ---- | ----
J9, J10, J14, J15, J16, J17, J26, J27 | 8 |  | Header, 2.54 mm, 3x1, Gold, TH | Header, 2.54mm, 3x1, TH | 61300311121 | Wurth Elektronik | ---- | ----
J11 | 1 |  | Header, 1.27mm, 7x2, Gold, SMT | Header, 1.27mm, 7x2, SMT | FTSH-107-01-F-DV | Samtec | ---- | ----
J12, J18, J19, J20, J21, J22, J23, J24, J25, J28 | 10 |  | Header, 2.54 mm, 2x1, Gold, TH | Header, 2.54mm, 2x1, TH | 61300211121 | Wurth Elektronik | ---- | ----
L3 | 1 | 3.9nH | Inductor, Multilayer, Air Core, 3.9 nH, 0.75 A, 0.14 ohm, SMD | 0402 polarized | LQG15HS3N9S02D | MuRata
L4 | 1 | 2.7nH | Inductor, Multilayer, Air Core, 2.7 nH, 0.9 A, 0.07 ohm, AEC-Q200 Grade 1, SMD | 0402 | LQG15WH2N7C02D | MuRata
L5, L6 | 2 | 10 ohm | Ferrite Bead, 10 ohm @ 100 MHz, 1 A, 0402 | 0402 | BLM15AG100SN1D | MuRata | ---- | ----
L7, L10 | 2 | 2.2uH | Inductor, Multilayer, Ferrite, 2.2 uH, 1.2 A, 0.11 ohm, SMD | 2.0x1.6mm | LQM2MPN2R2NG0 | MuRata | ---- | ----
L9 | 1 | 1uH | Inductor, Multilayer, Ferrite, 1 uH, 1.6 A, 0.055 ohm, SMD | SMD, Body 2.5x2mm, Height 1.2mm | LQM2HPN1R0MG0L | MuRata | ---- | ----
L12 | 1 | 2.2uH | Inductor, Wirewound, 2.2 uH, 1 A, 0.143 ohm, SMD | 0805 | BRC2012T2R2MD | Taiyo Yuden | ---- | ----
Label1 | 1 |  | Thermal Transfer Printable Labels, 0.650" W x 0.200" H - 10,000 per roll | PCB Label 0.650 x 0.200 inch | THT-14-423-10 | Brady | ---- | ----
P1, P2 | 2 |  | Receptacle, 2.54 mm, 10x2, Gold, TH | Receptacle, 2.54 mm, 10x2, TH | CRD-081413-A-G | Major League Electronics | Order Directly from Major League
PCB1 | 1 |  | Printed Circuit Board |  | MCU014 | Any | ---- | ----
Q1, Q4, Q5, Q7 | 4 | 50V | MOSFET, N-CH, 50 V, 0.22 A, SOT-23 | SOT-23 | BSS138 | Fairchild Semiconductor | BSS138LT1G | ON
Q2 | 1 | -50V | MOSFET, 2-CH, P-CH, -50 V, -0.13 A, AEC-Q101, SOT-363 | SOT-363 | BSS84DW-7-F | Diodes Inc. | ---- | ----
Q3 | 1 | -30V | MOSFET, P-CH, -30 V, -1.5 A, SSOT-3 | SSOT-3 | FDN358P | Fairchild Semiconductor | ---- | ----
R1 | 1 | 0 | RES, 0, 5%, 0.05 W, 0201 | 0201 | CRCW02010000Z0ED | Vishay-Dale
R2, R4, R6, R43, R47, R48, R49, R50, R54, R60, R61, R69, R71, R73, R76, R77, R79, R80, R81, R83, R84, R85, R87, R89, R90, R91, R92, R93, R94, R95, R96, R97, R98, R99, R100, R101, R125, R130, R131, R132, R138, R139, R140, R145, R146, R147, R148, R149, R165, R167, R168 | 51 | 0 | RES, 0, 5%, 0.063 W, 0402 | 0402 | ERJ-2GE0R00X | Panasonic | RC0402JR-070RL | YAGEO
R5, R7, R9, R10, R11, R12, R13, R34, R36 | 9 | 33.0 | RES, 33.0, 1%, 0.1 W, 0402 | 0402 | ERJ-2RKF33R0X | Panasonic | RC0402FR-0733RL | YAGEO
R8 | 1 | 100 | RES, 100, 5%, 0.063 W, AEC-Q200 Grade 0, 0402 | 0402 | CRCW0402100RJNED | Vishay-Dale | RC0402JR-07100RL | YAGEO
R15 | 1 | 330k | RES, 330 k, 5%, 0.063 W, AEC-Q200 Grade 0, 0402 | 0402 | CRCW0402330KJNED | Vishay-Dale | RC0402JR-07330KL | YAGEO
R16 | 1 | 220k | RES, 220 k, 5%, 0.063 W, AEC-Q200 Grade 0, 0402 | 0402 | CRCW0402220KJNED | Vishay-Dale | RC0402JR-07220KL | YAGEO
R17, R26, R59, R154, R155, R156, R157 | 7 | 10k | RES, 10 k, 5%, 0.063 W, AEC-Q200 Grade 0, 0402 | 0402 | CRCW040210K0JNED | Vishay-Dale | RC0402JR-0710KL | YAGEO
R18, R19 | 2 | 220 | RES, 220, 5%, 0.1 W, AEC-Q200 Grade 0, 0603 | 0603 | CRCW0603220RJNEA | Vishay-Dale | RC0603JR-07220RL | YAGEO
R20, R158, R160 | 3 | 270 | RES, 270, 5%, 0.1 W, AEC-Q200 Grade 0, 0603 | 0603 | CRCW0603270RJNEA | Vishay-Dale | RC0603JR-07270RL | YAGEO
R21 | 1 | 100 | RES, 100, 1%, 0.1 W, 0402 | 0402 | ERJ-2RKF1000X | Panasonic | RC0402FR-07100RL | YAGEO
R22, R23, R24, R25, R28, R31, R35, R37, R150, R151, R159 | 11 | 1.0k | RES, 1.0 k, 5%, 0.063 W, AEC-Q200 Grade 0, 0402 | 0402 | CRCW04021K00JNED | Vishay-Dale | RC0402JR-071KL | YAGEO
R27 | 1 | 100k | RES, 100 k, 5%, 0.1 W, AEC-Q200 Grade 0, 0603 | 0603 | CRCW0603100KJNEA | Vishay-Dale | RC0603JR-07100KL | YAGEO
R29 | 1 | 100 | RES, 100, 1%, 0.063 W, AEC-Q200 Grade 0, 0402 | 0402 | CRCW0402100RFKED | Vishay-Dale | RC0402FR-07100RL | YAGEO
R30 | 1 | 4.87k | RES, 4.87 k, 1%, 0.1 W, AEC-Q200 Grade 0, 0603 | 0603 | CRCW06034K87FKEA | Vishay-Dale | RC0603FR-074K87L | YAGEO
R32 | 1 | 51 | RES, 51, 5%, 0.063 W, AEC-Q200 Grade 0, 0402 | 0402 | CRCW040251R0JNED | Vishay-Dale | RC0402JR-0751RL | YAGEO
R33, R41, R44, R56, R62, R63, R152, R161, R169, R170, R171 | 11 | 100k | RES, 100 k, 5%, 0.063 W, AEC-Q200 Grade 0, 0402 | 0402 | CRCW0402100KJNED | Vishay-Dale | RC0402JR-07100KL | YAGEO
R38, R39 | 2 | 33 | RES, 33, 5%, 0.1 W, AEC-Q200 Grade 0, 0603 | 0603 | CRCW060333R0JNEA | Vishay-Dale | RC0603JR-0733RL | YAGEO
R40, R66, R166 | 3 | 0 | RES, 0, 5%, 0.1 W, 0603 | 0603 | ERJ-3GEY0R00V | Panasonic | RC0603FR-070RL | YAGEO
R51 | 1 | 270 | RES, 270, 5%, 0.063 W, AEC-Q200 Grade 0, 0402 | 0402 | CRCW0402270RJNED | Vishay-Dale | RC0402JR-07270RL | YAGEO
R52, R53, R57, R58 | 4 | 69.8k | RES, 69.8 k, 1%, 0.063 W, AEC-Q200 Grade 0, 0402 | 0402 | CRCW040269K8FKED | Vishay-Dale | RC0402FR-0769K8L | YAGEO
R55 | 1 | 2.2k | RES, 2.2 k, 5%, 0.063 W, AEC-Q200 Grade 0, 0402 | 0402 | CRCW04022K20JNED | Vishay-Dale | RC0402JR-072K2L | YAGEO
R114, R116, R122, R124 | 4 | 470 | RES, 470, 1%, 0.1 W, AEC-Q200 Grade 0, 0402 | 0402 | ERJ-2RKF4700X | Panasonic | RC0402FR-07470RL | YAGEO
R115, R117, R126, R127 | 4 | 576k | RES, 576 k, 1%, 0.063 W, AEC-Q200 Grade 0, 0402 | 0402 | CRCW0402576KFKED | Vishay-Dale | RC0402FR-07576KL | YAGEO
R118, R119, R128, R129 | 4 | 422k | RES, 422 k, 1%, 0.063 W, AEC-Q200 Grade 0, 0402 | 0402 | CRCW0402422KFKED | Vishay-Dale | RC0402FR-07422KL | YAGEO
R133, R134 | 2 | 3.3k | RES, 3.3 k, 5%, 0.063 W, AEC-Q200 Grade 0, 0402 | 0402 | CRCW04023K30JNED | Vishay-Dale | RC0402JR-073K3L | YAGEO
R153 | 1 | 100k | RES, 100 k, 1%, 0.1 W, 0402 | 0402 | ERJ-2RKF1003X | Panasonic | RC0402FR-07100KL | YAGEO
R162, R163, R164 | 3 | 750 | RES, 750, 5%, 0.1 W, 0603 | 0603 | RC0603JR-07750RL | Yageo America | ---- | ----
SH-J3, SH-J4, SH-J5, SH-J6, SH-J7, SH-J8, SH-J9, SH-J10, SH-J11, SH-J12, SH-J13, SH-J14, SH-J15, SH-J16, SH-J17, SH-J18, SH-J19, SH-J20, SH-J21, SH-J22, SH-J23 | 21 |  | Shunt, 2.54mm, Gold, Black | Shunt, 2.54mm, Black | 60900213421 | Wurth Elektronik | ---- | ----
SW1, SW2, SW3 | 3 |  | Switch, SPST, 0.05 A, 12 VDC, SMD | 7.8x3.5mm | 1188E-1K2-V-TR | Diptronics | ---- | ----
SW4 | 1 |  | Switch, SPST-NO, Off-Mom, 0.05 A, 12 VDC, SMT | 3x2.5mm | B3U-3000P | Omron Electronic Components
TP2 | 1 |  | Test Point, Miniature, SMT | Testpoint_Keystone_Miniature | 5015 | Keystone | ---- | ----
U1 | 1 |  | Multilayer Diplexer for 2.4GHz W-LAN & Bluetooth / 5GHz W-LAN | 1.6x0.8mm | DPX165950DT-8148A1 | TDK | ---- | ----
U2 | 1 |  | 0.03 GHz-6 GHz SPDT Switch | 1x1mm | RTC6608OSP | Richwave | Order Directly from Richwave | ----
U3 | 1 |  | Tiva C Series Microcontroller, 1024 KB Flash, 256 KB SRAM, 12 Bit, 20 Channels, -40 to 85 degC, 128-Pin TQFP (PDT), Green (RoHS & no Sb/Br), Tape and Reel | PDT0128A | TM4C1294NCPDTI3R | Texas Instruments | ---- | ----
U4, U7, U8 | 3 |  | Single-Bit Dual-Supply Bus Transceiver with Configurable Voltage Translation and 3-State Outputs, DCK0006A, LARGE T&R | DCK0006A | SN74LVC1T45DCKR | Texas Instruments | SN74LVC1T45DCKT | Texas Instruments
U5 | 1 |  | ESD Solution for High-Speed Differential Interface, 4 Channels, -40 to +85 degC,10-pin SON (DQA), Green (RoHS & no Sb/Br) | DQA0010A | TPD4S010DQAR | Texas Instruments | ---- | ----
U6 | 1 |  | Precision Micropower Shunt Voltage Reference, 0.2% accuracy, 2.5 V, 15 ppm / degC, 15 mA, -40 to 85 degC, 3-pin SOT-23 (DBZ), Green (RoHS & no Sb/Br) | DBZ0003A | LM4040B25IDBZR | Texas Instruments | ---- | ----
U9 | 1 |  | ULTRA LOW POWER, 32M-BIT [x 1/x 2/x 4] CMOS MXSMIO(SERIAL MULTI I/O) FLASH MEMORY, SOP-8 | 8-SOP | MX25R3235FM1IL0 | Macronix International Co., LTD | ---- | ----
U10 | 1 |  | SimpleLink Wi-Fi and Internet-of-Things Solution, a Single-Chip Wireless MCU, RGK0064B (VQFN-64) | RGK0064B | CC3235SM2RGKR | Texas Instruments | CC3235SM2RGKT | Texas Instruments
U11 | 1 |  | Low Cost, Low Power, Rail-to-Rail Operational Amplifier MicroAmplifier(TM) Series, 2.7 to 5.5 V, -55 to 125 degC, 14-pin SOP (PW14), Green (RoHS & no Sb/Br) | PW0014A | OPA4342EA/250 | Texas Instruments | ---- | ----
U12 | 1 |  | High-Accuracy, Low-Power, Digital Temperature Sensor with SMBus and Two-Wire Serial Interface, DRV0006A (WSON-6) | DRV0006A | TMP116AIDRVR | Texas Instruments | TMP116AIDRVT | Texas Instruments
U13 | 1 |  | 14 Bit, Digital, Triaxial Acceleration Sensor with Intelligent On-Chip Motion-Triggered Interrupt Controller, 12LGA | LGA, 12-Leads, Body 2x2mm, Pitch 0.5mm | BMA280 | Bosch Solar Energy
U14 | 1 |  | Buck Step Down Regulator with 3 to 17 V Input and 3.3 V Output, -40 to 85 degC, 8-Pin WSON (DSG), Green (RoHS & no Sb/Br) | DSG0008A | TPS62162DSGR | Texas Instruments | ---- | ----
Y1 | 1 |  | Crystal, 16 MHz, 18 pF, SMD | ABM3 | ABM3-16.000MHZ-D2Y-T | Abracon Corporation | ---- | ----
Y2 | 1 |  | CRYSTAL, 32.768KHz, 9PF, SMD | 3.2x0.9x1.5mm | ABS07-32.768KHZ-9-T | Abracon Corporation | ---- | ----
Y3 | 1 |  | Crystal, 40 MHz, 8 pF, SMD | 2x1.6mm | 8Y40072002 | TXC Corporation | Order Directly from TXC | ----
C1 | 0 | 10pF | CAP, CERM, 10 pF, 50 V, +/- 5%, C0G/NP0, 0402 | 0402 | GRM1555C1H100JA01D | MuRata | GRM1555C1H100JA01D | ----
C3, C4, C5 | 0 | 0.5pF | CAP, CERM, 0.5 pF, 50 V,+/- 20%, C0G/NP0, 0402 | 0402 | GJM1555C1HR50BB01J | MuRata
C11 | 0 | 1pF | CAP, CERM, 1 pF, 50 V, +/- 10%, C0G/NP0, 0402 | 0402 | GRM1555C1H1R0BA01D | MuRata | ---- | ----
J1 | 0 |  | Connector, SMA, Vertical, Gold, SMT | SMD, 4-Leads, Body 7.1x7.1mm | SMA-10V21-TGG | Hus-Tsan Group Co., Ltd. | SMA-050710 | 傲创
L1 | 0 | 22nH | Inductor, Multilayer, Air Core, 22 nH, 0.35 A, 0.42 ohm, AEC-Q200 Grade 1, SMD | 0402 | LQG15HZ22NH02D | MuRata
L2 | 0 | 6.8nH | Inductor, Multilayer, Air Core, 6.8 nH, 0.6 A, 0.22 ohm, AEC-Q200 Grade 1, SMD | 0402 | LQG15HZ6N8H02D | MuRata
L11 | 0 | 10uH | Inductor, Multilayer, Ferrite, 10 uH, 0.7 A, 0.364 ohm, SMD | Inductor, 2.5x0.85x2mm | MLP2520S100MT0S1 | TDK | ---- | ----
Q6 | 0 | -30V | MOSFET, P-CH, -30 V, -1.5 A, SSOT-3 | SSOT-3 | FDN358P | Fairchild Semiconductor | ---- | ----
R3, R42, R65, R67, R68, R70, R72, R74, R75, R78, R82, R86, R88, R102, R103, R104, R105, R106, R107, R108, R109, R110, R111, R112, R113, R120, R121, R123, R135, R136, R137, R142, R143, R144, R172 | 0 | 0 | RES, 0, 5%, 0.063 W, 0402 | 0402 | ERJ-2GE0R00X | Panasonic | RC0402JR-070RL | YAGEO
R14, R45, R46 | 0 | 100k | RES, 100 k, 5%, 0.063 W, AEC-Q200 Grade 0, 0402 | 0402 | CRCW0402100KJNED | Vishay-Dale | RC0402JR-07100KL | YAGEO
R64 | 0 | 0 | RES, 0, 5%, 0.1 W, 0603 | 0603 | ERJ-3GEY0R00V | Panasonic | RC0603FR-070RL | YAGEO
R141 | 0 | 0 | RES, 0, 5%, 0.125 W, 0805 | 0805 | ERJ-6GEY0R00V | Panasonic | ---- | ----
 |  | Notes:
 |  | Unless otherwise noted in the Alternate PartNumber and/or Alternate Manufacturer columns, all parts may be substituted with equivalents.

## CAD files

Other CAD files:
ccs_workspace/tirtos_builds_cc32xx_release_ccs/src/sysbios/m3_IntrinsicsSupport_asm.obj
ccs_workspace/tirtos_builds_MSP_EXP432P401R_release_ccs/src/sysbios/m3_IntrinsicsSupport_asm.obj
ccs_workspace/tirtos_builds_MSP_EXP432P401R_release_ccs/src/sysbios/m3_Hwi_asm_switch.obj
ccs_workspace/tirtos_builds_cc32xx_release_ccs/src/sysbios/m3_Hwi_asm.obj
ccs_workspace/tirtos_builds_MSP_EXP432P401R_release_ccs/src/sysbios/m3_TaskSupport_asm.obj
ccs_workspace/tirtos_builds_cc32xx_release_ccs/src/sysbios/m3_TaskSupport_asm.obj
ccs_workspace/tirtos_builds_MSP_EXP432P401R_release_ccs/src/sysbios/m3_Hwi_asm.obj
ccs_workspace/tirtos_builds_cc32xx_release_ccs/src/sysbios/m3_Hwi_asm_switch.obj
ccs_workspace/tirtos_builds_cc32xx_release_ccs/src/sysbios/BIOS.obj
ccs_workspace/tirtos_builds_MSP_EXP432P401R_release_ccs/src/sysbios/BIOS.obj

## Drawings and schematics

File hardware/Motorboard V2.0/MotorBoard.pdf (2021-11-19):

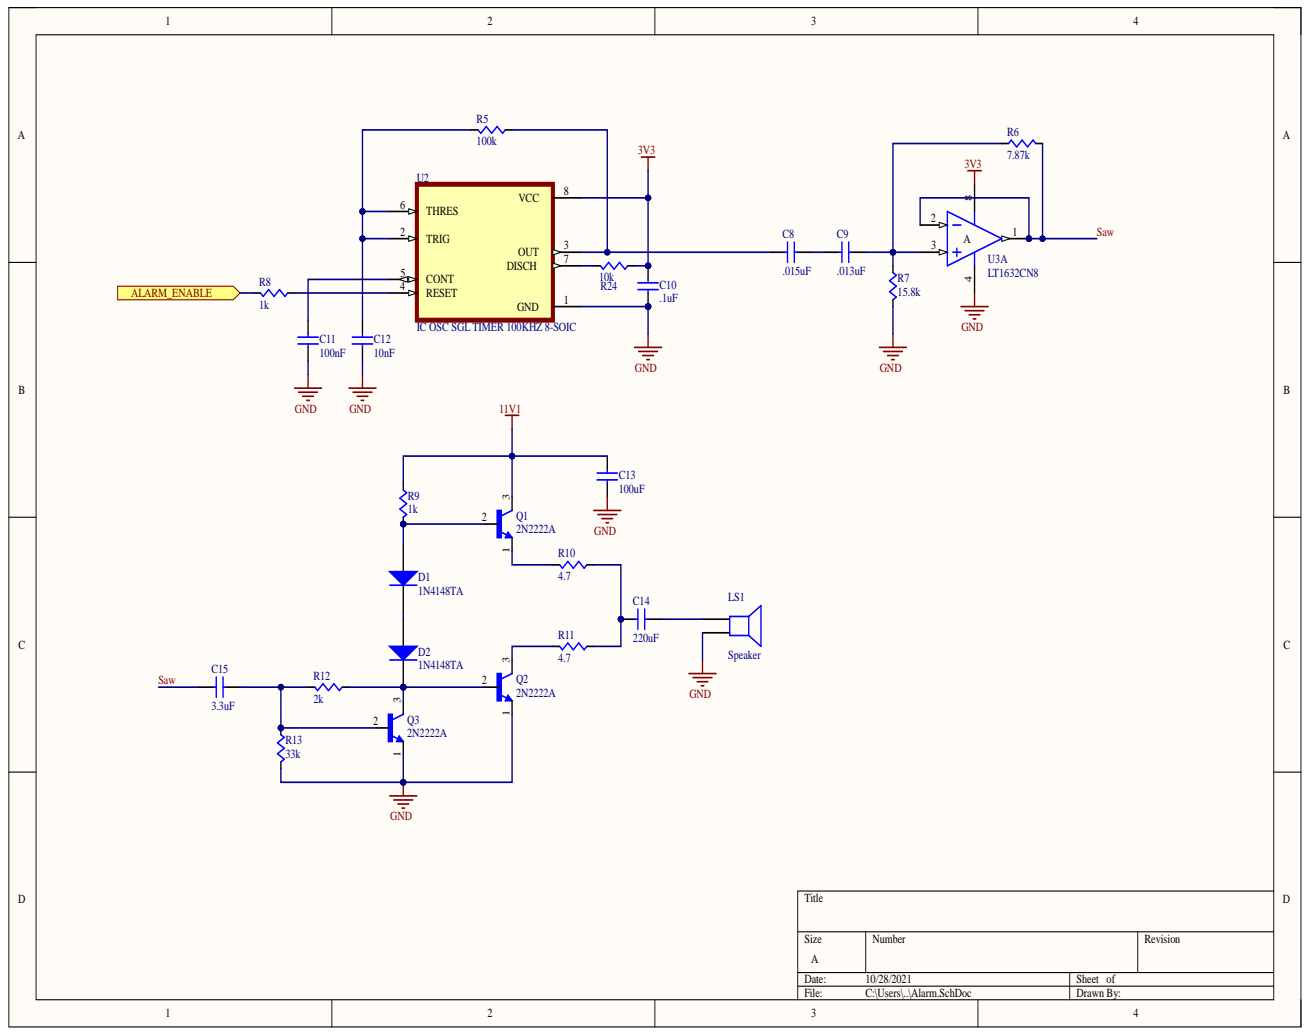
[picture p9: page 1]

IC OSC SGL TIMER 100KHZ 8-SOIC

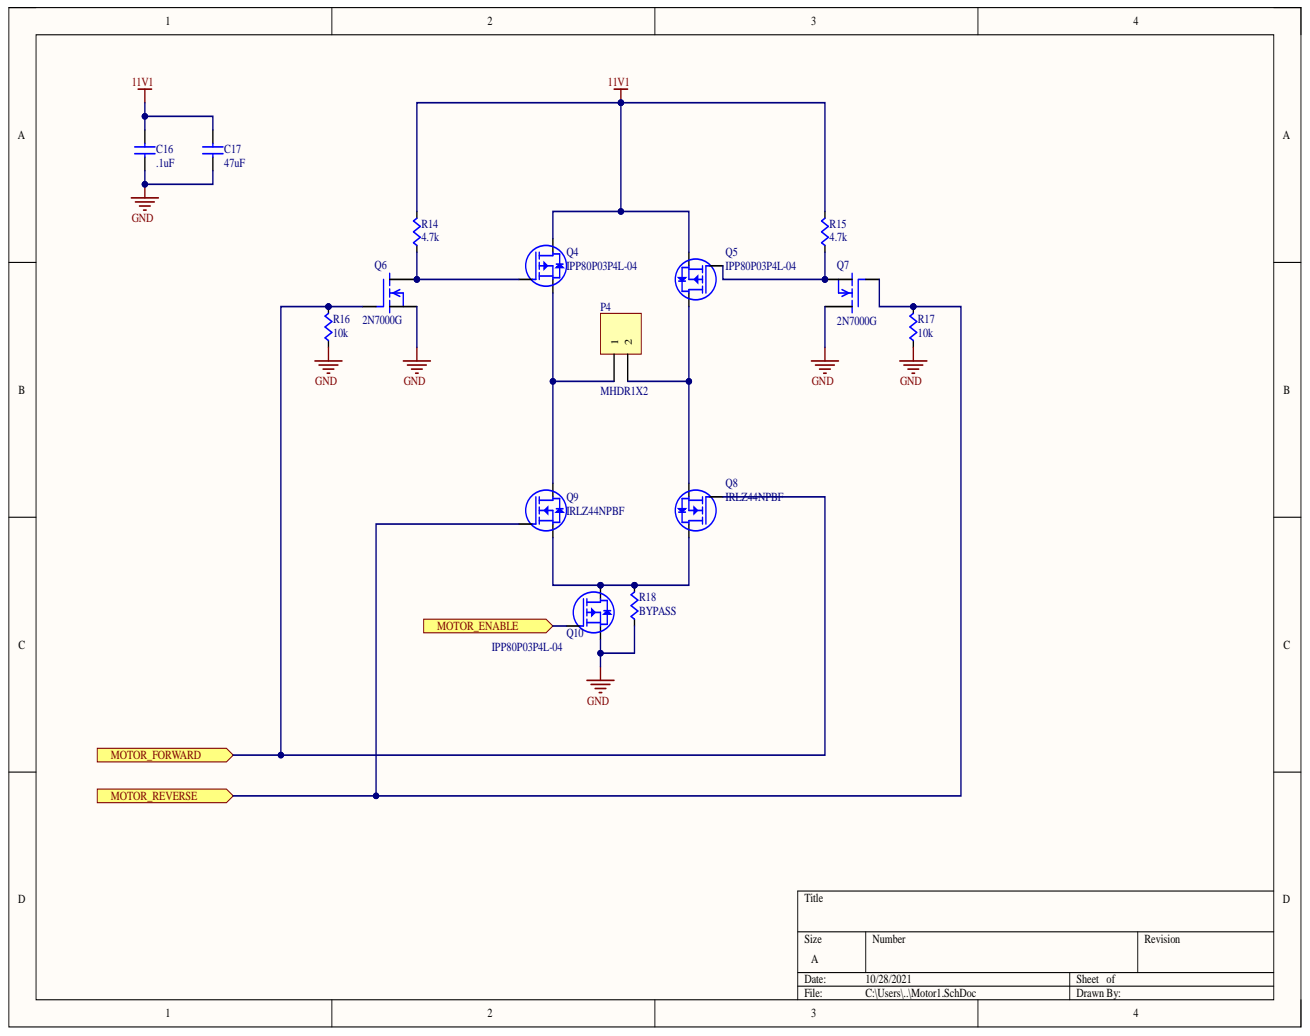
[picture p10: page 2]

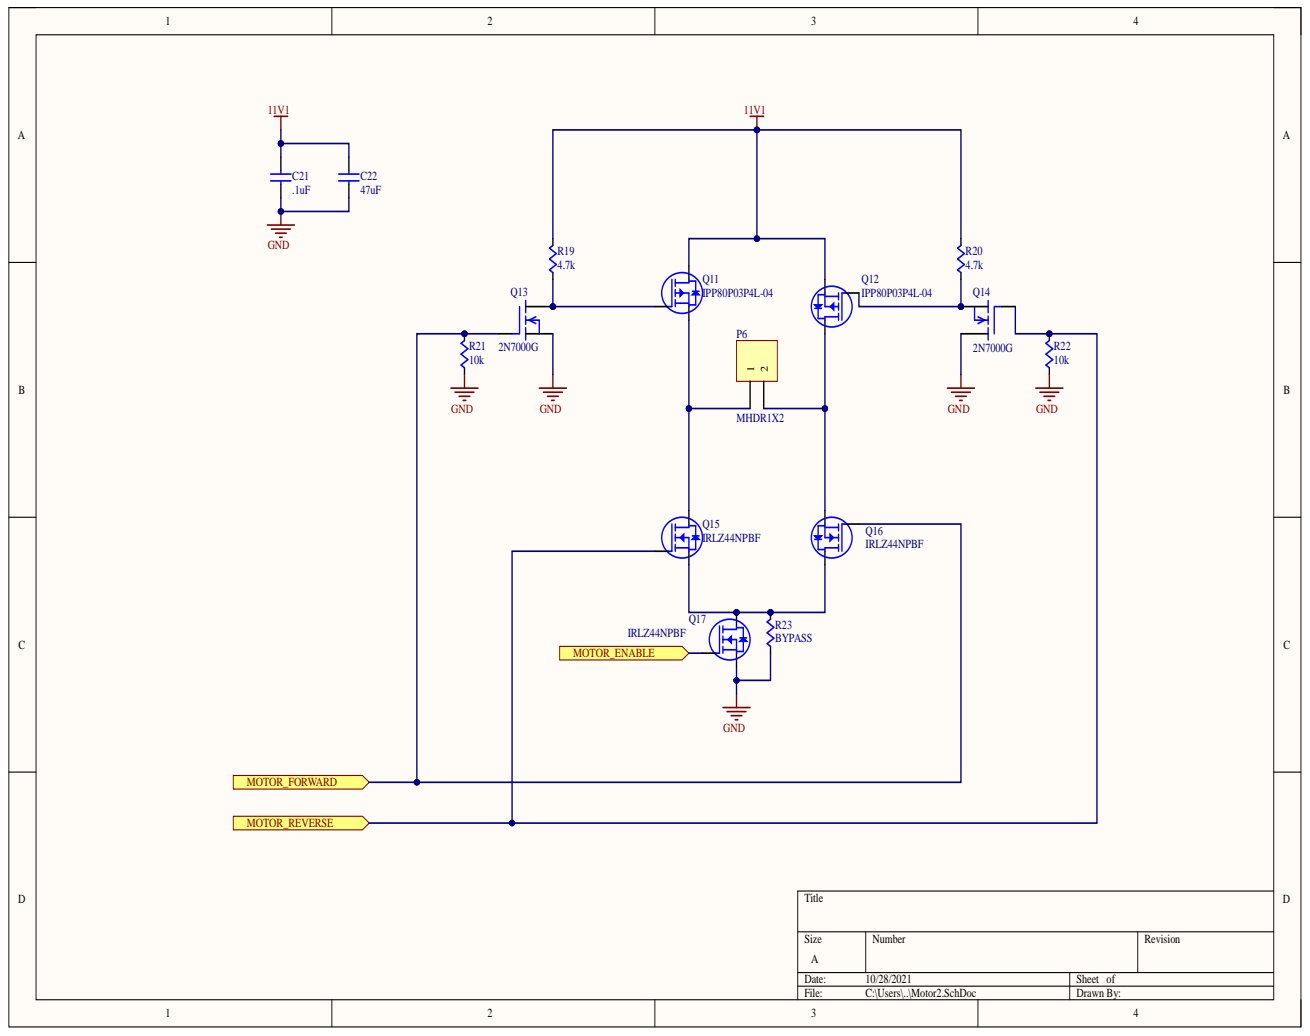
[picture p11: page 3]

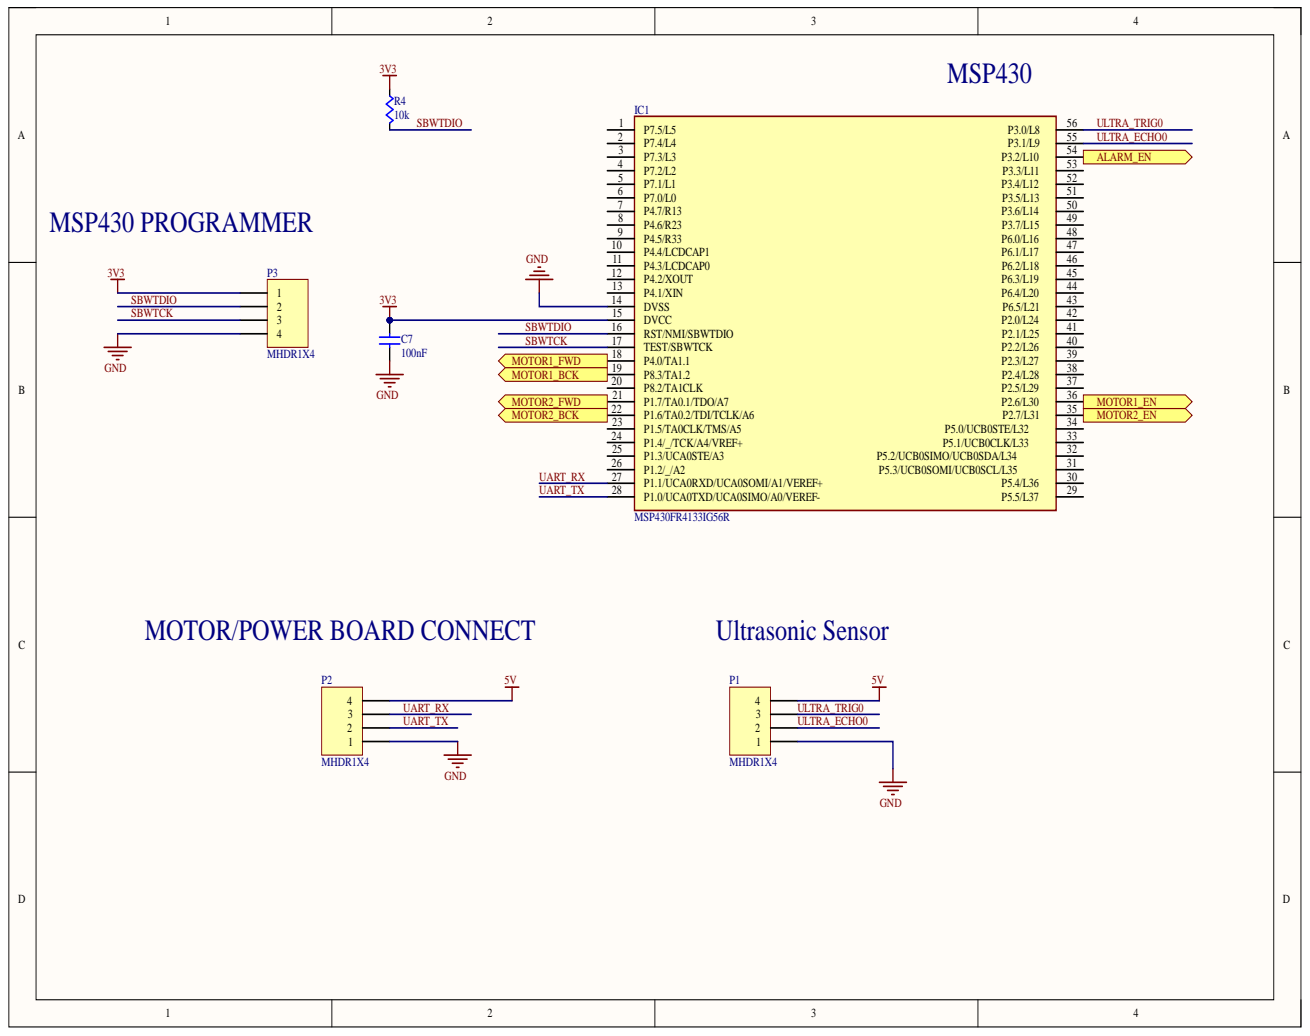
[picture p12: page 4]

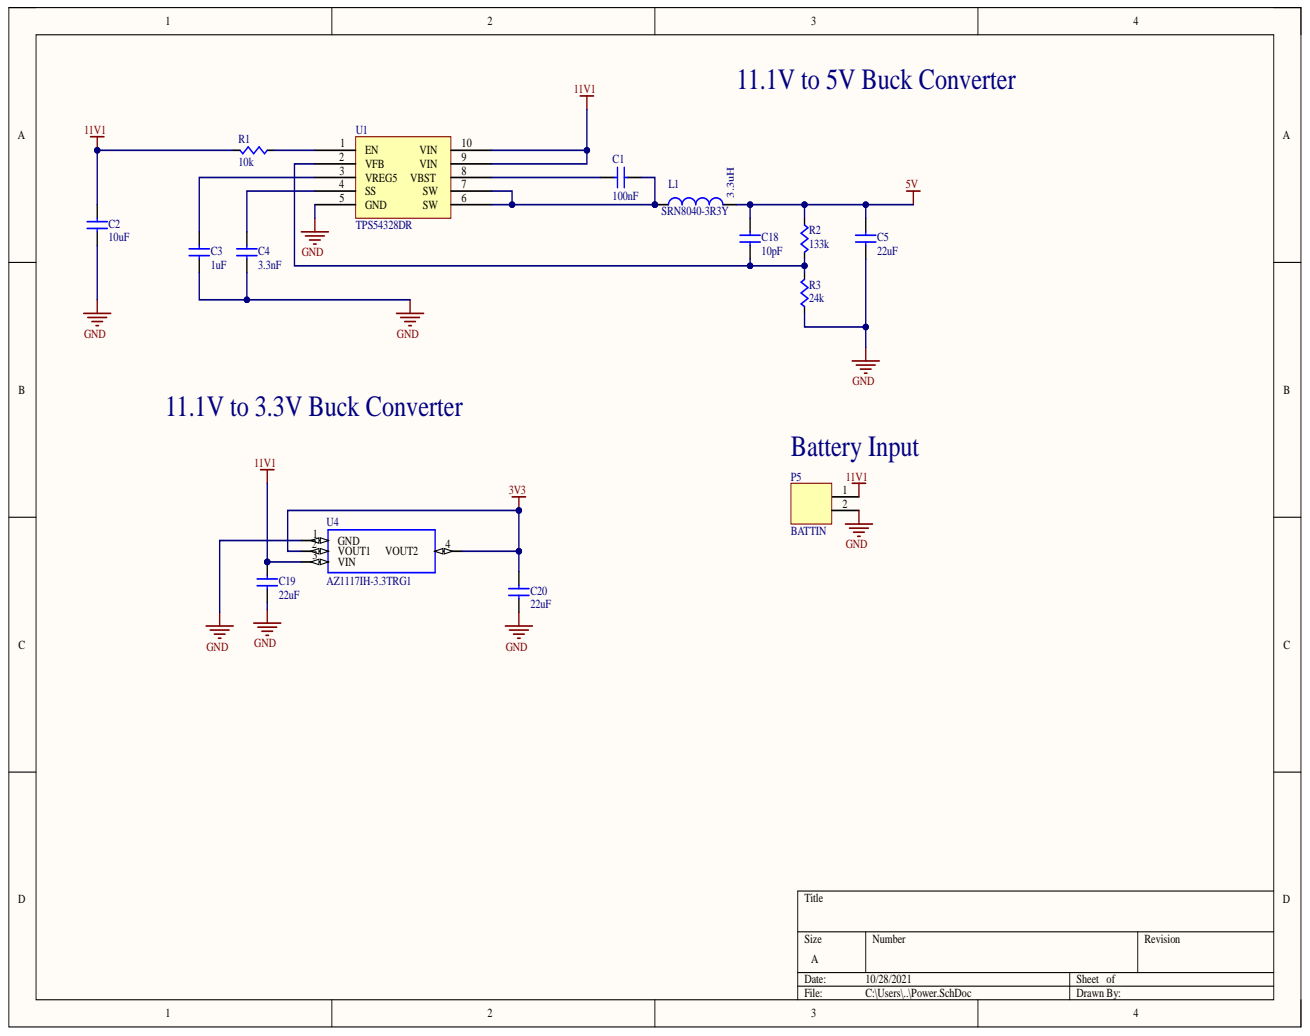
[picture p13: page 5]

3 | VREG 5 S S GND

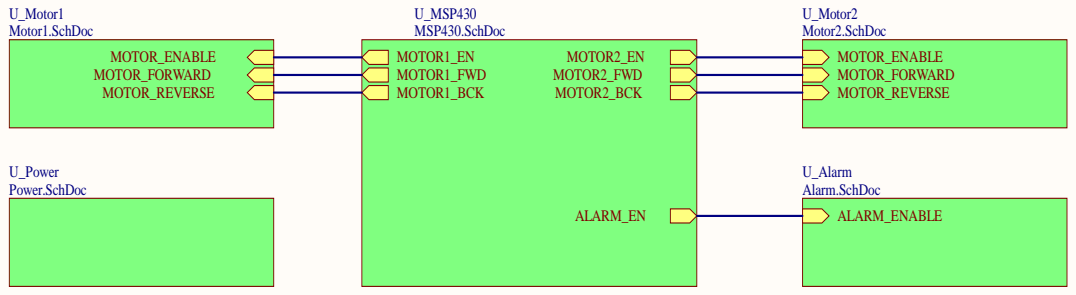
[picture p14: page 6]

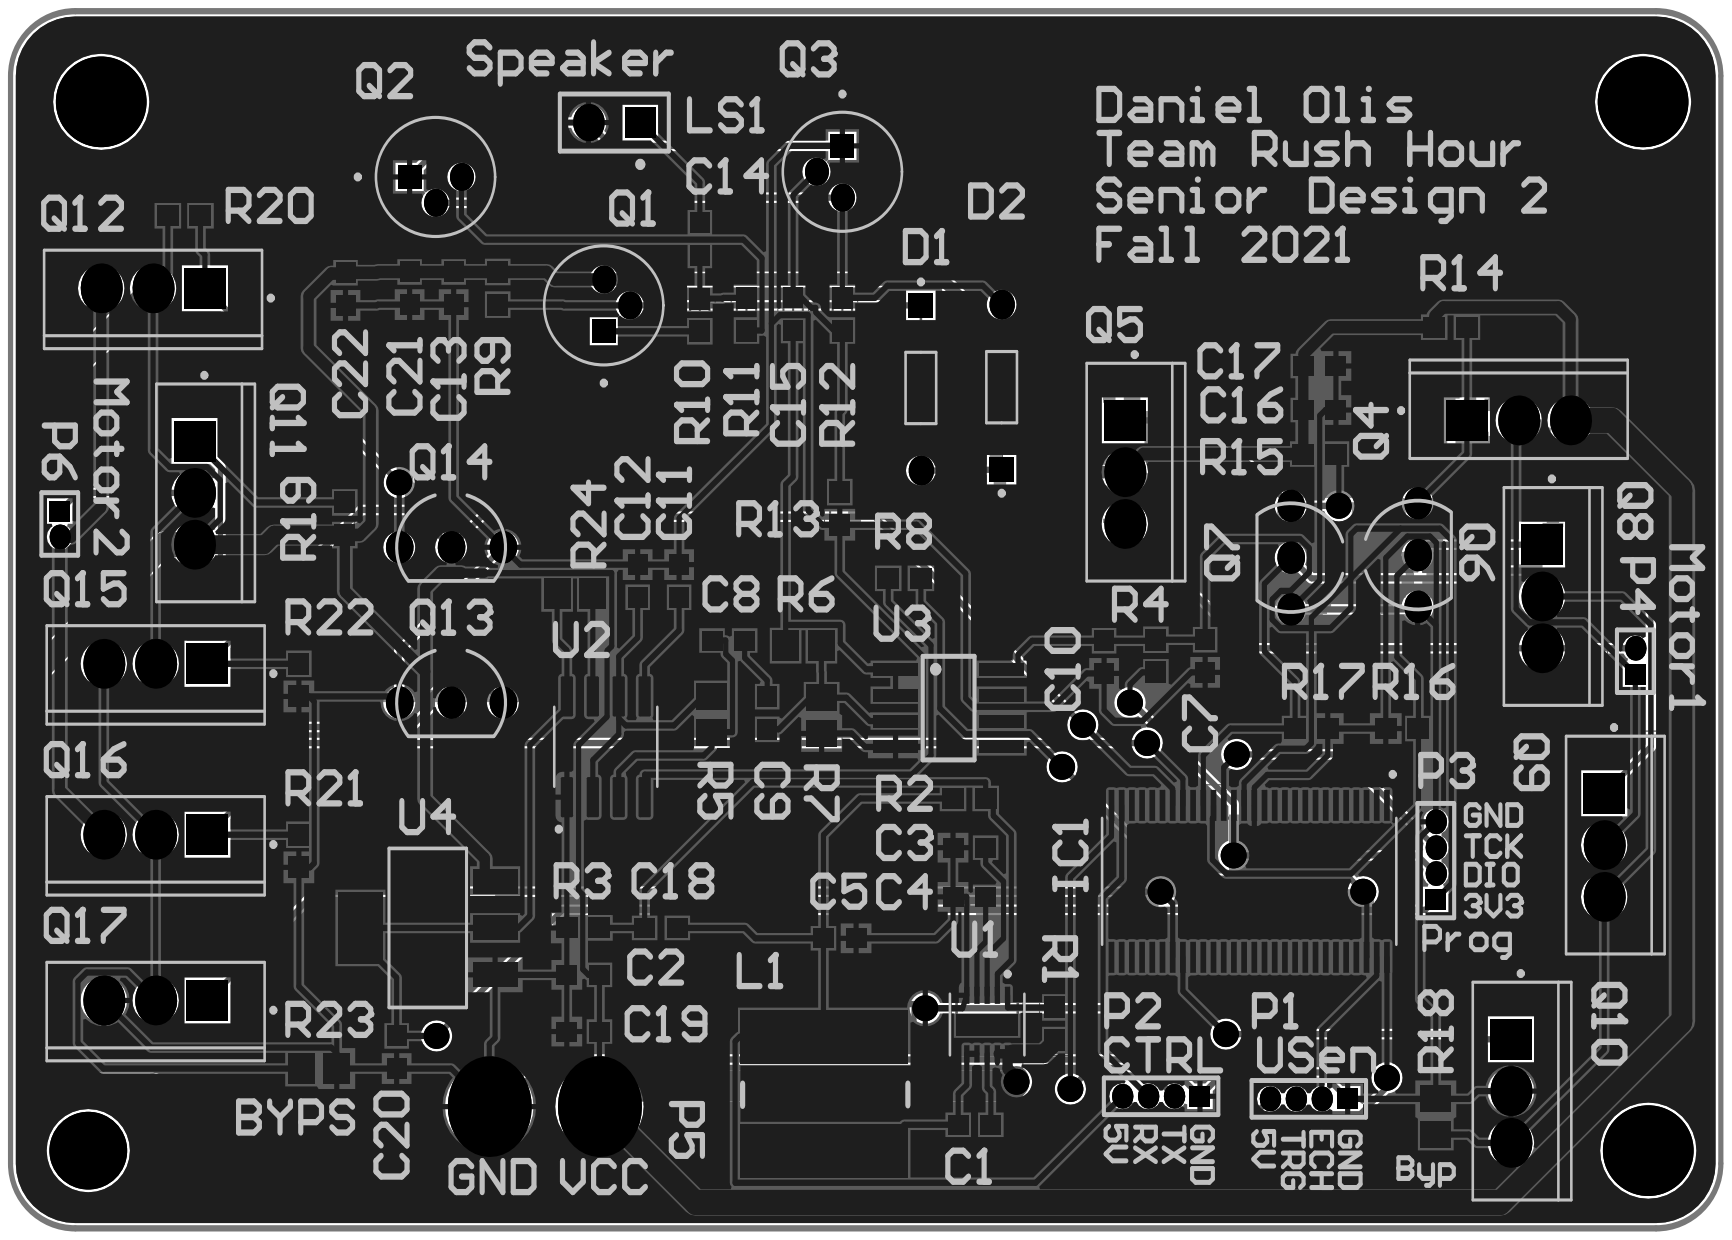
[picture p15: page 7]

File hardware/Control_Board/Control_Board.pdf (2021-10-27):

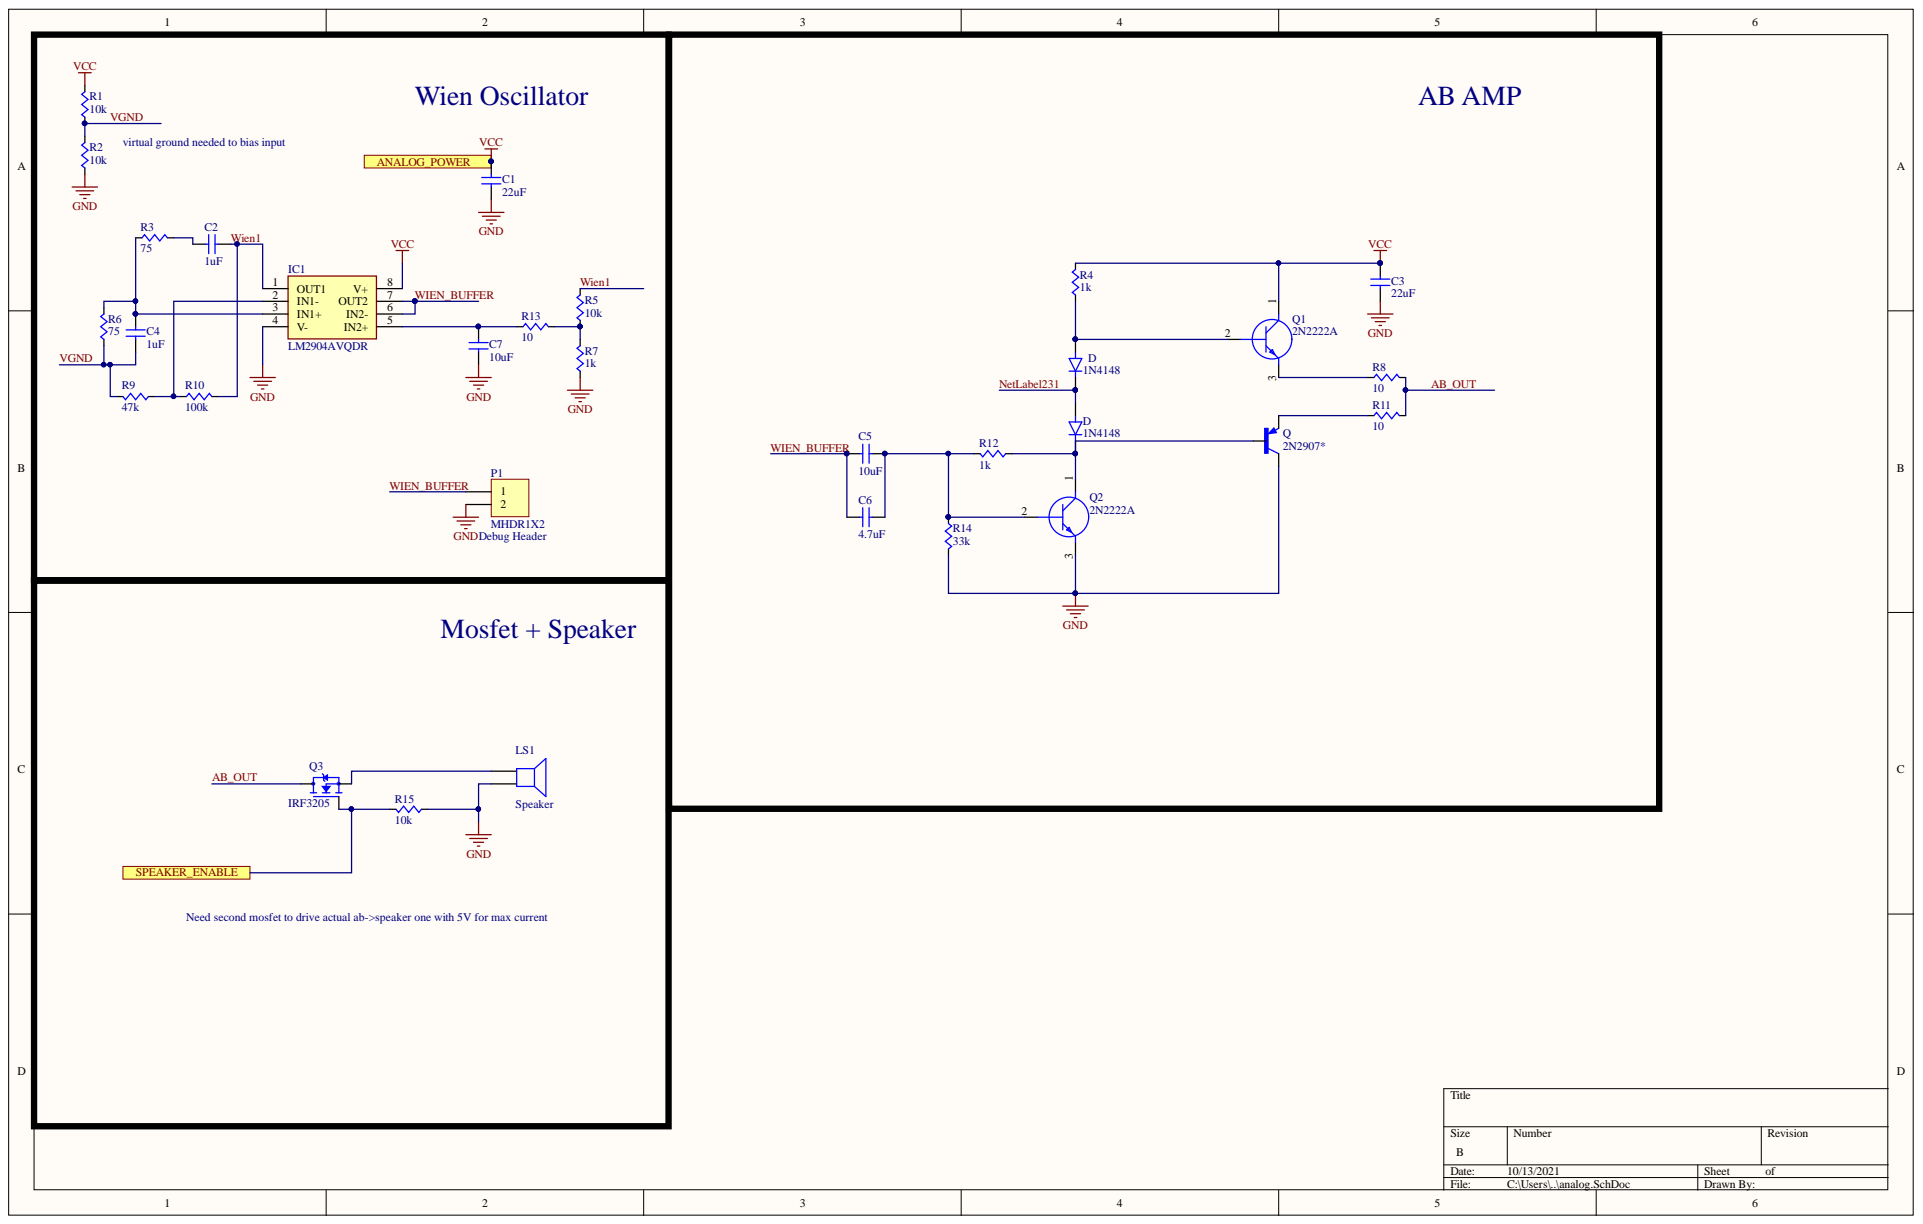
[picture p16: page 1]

VCC Wien Oscillator R1 VGND virtual ground needed to bias input VCC C2 | VCC

Need second mosfet to drive actual ab->speaker one with 5V for max current

Size B | Number | Revision

Date: 10/13/2021 | Sheet of
File: C:\Users\..\analog.SchDoc | Drawn By:

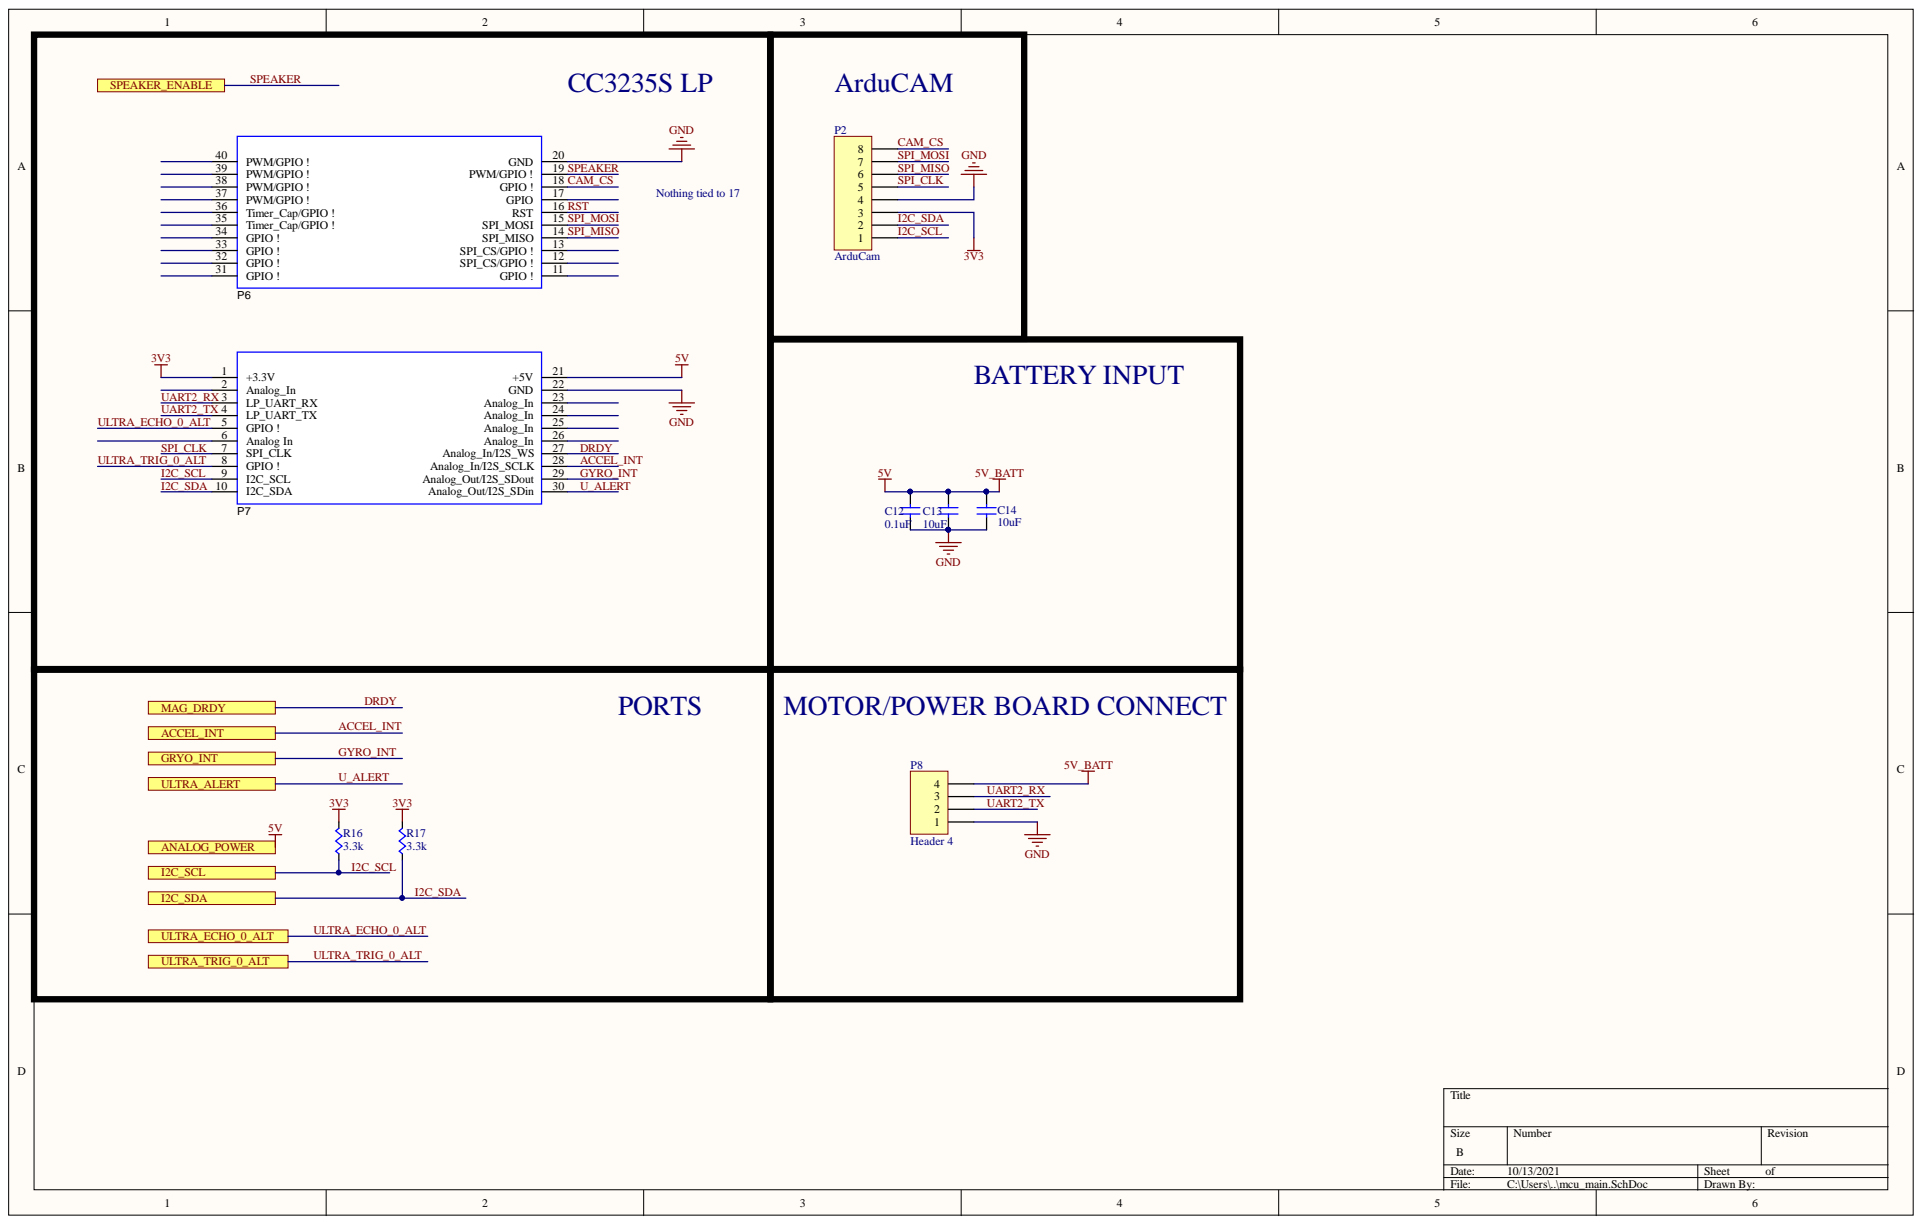
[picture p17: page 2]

GND | ArduCAM P2

MOTOR/POWER BOARD CONNECT

Size B | Number | Revision

Date: 10/13/2021 | Sheet of
File: C:\Users\..\mcu_main.SchDoc | Drawn By:

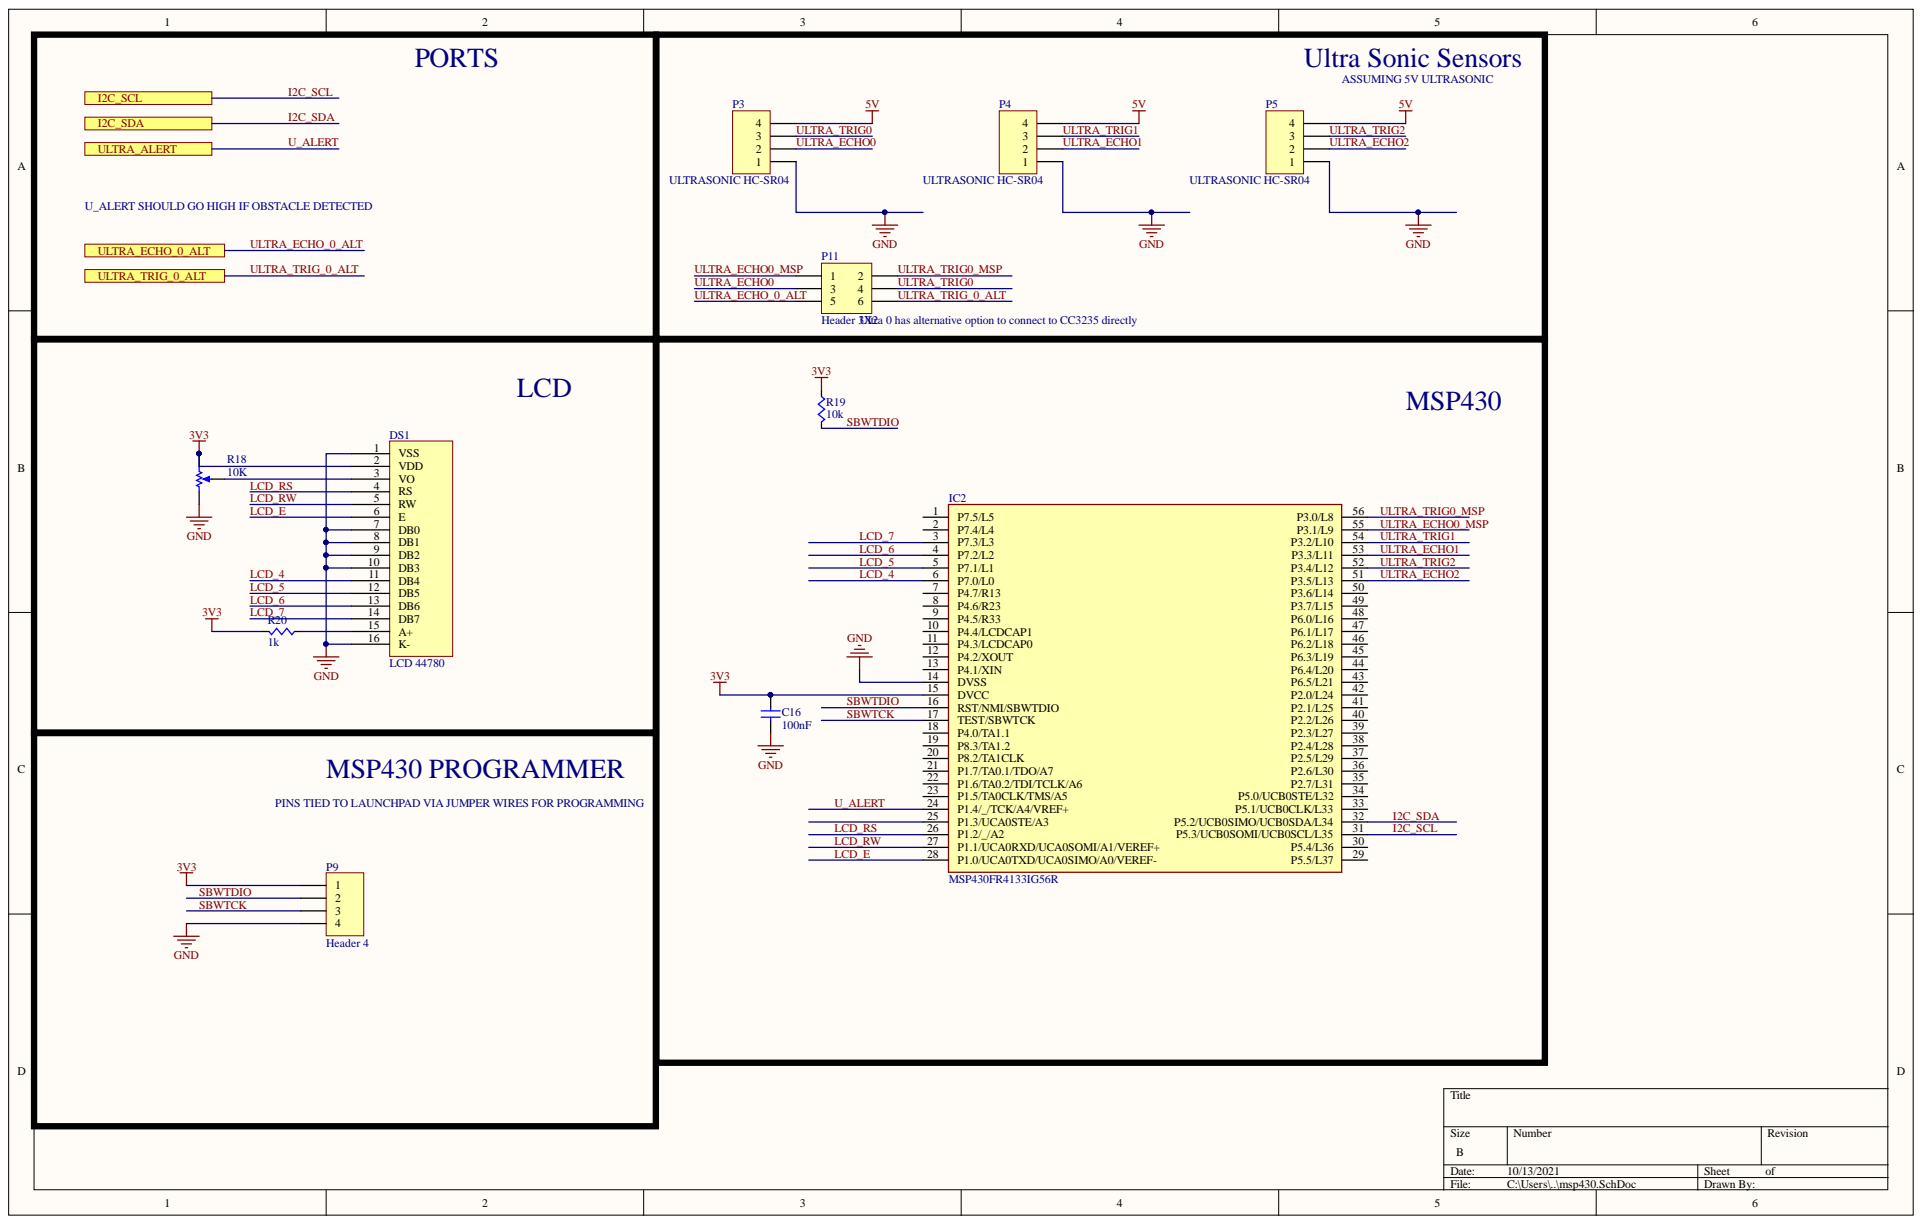
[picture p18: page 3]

PORTS U_ALERT SHOULD GO HIGH IF OBSTACLE DETECTED | Ultra Sonic Sensors ASSUMING 5V ULTRASONIC P3 5V P4 5V P5 5V Header 3XUlt2ra 0 has alternative option to connect to CC3235 directly

DB3 10
DB4 11 DB5 12 DB6 13 DB7 14 A+ 15 K- 16

Size B | Number | Revision

Date: 10/13/2021 | Sheet of
File: C:\Users\..\msp430.SchDoc | Drawn By:

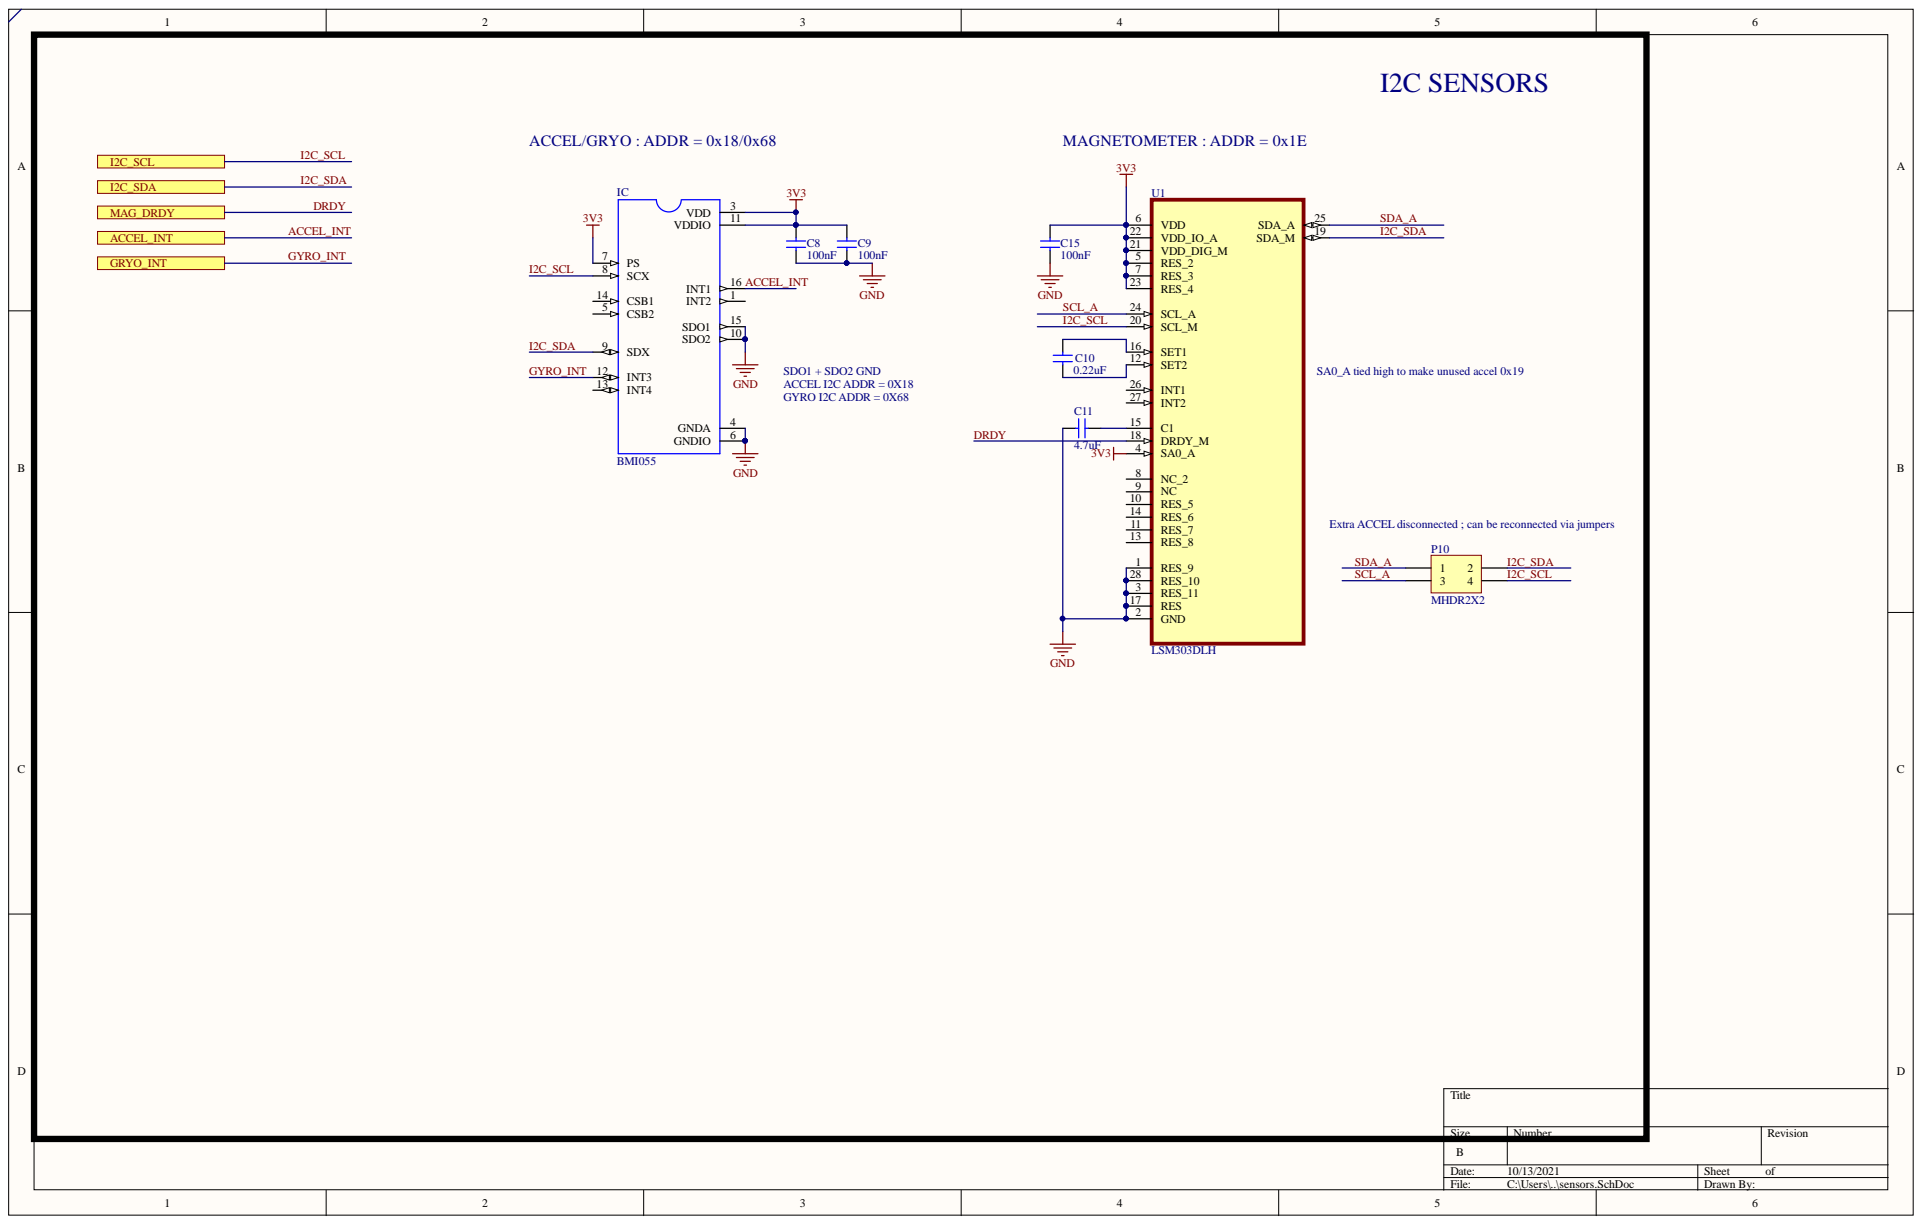
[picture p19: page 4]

ied high to make unused accel 0x19

sconnected ; can be reconnected via jumper

Size | Number | Revi s ion

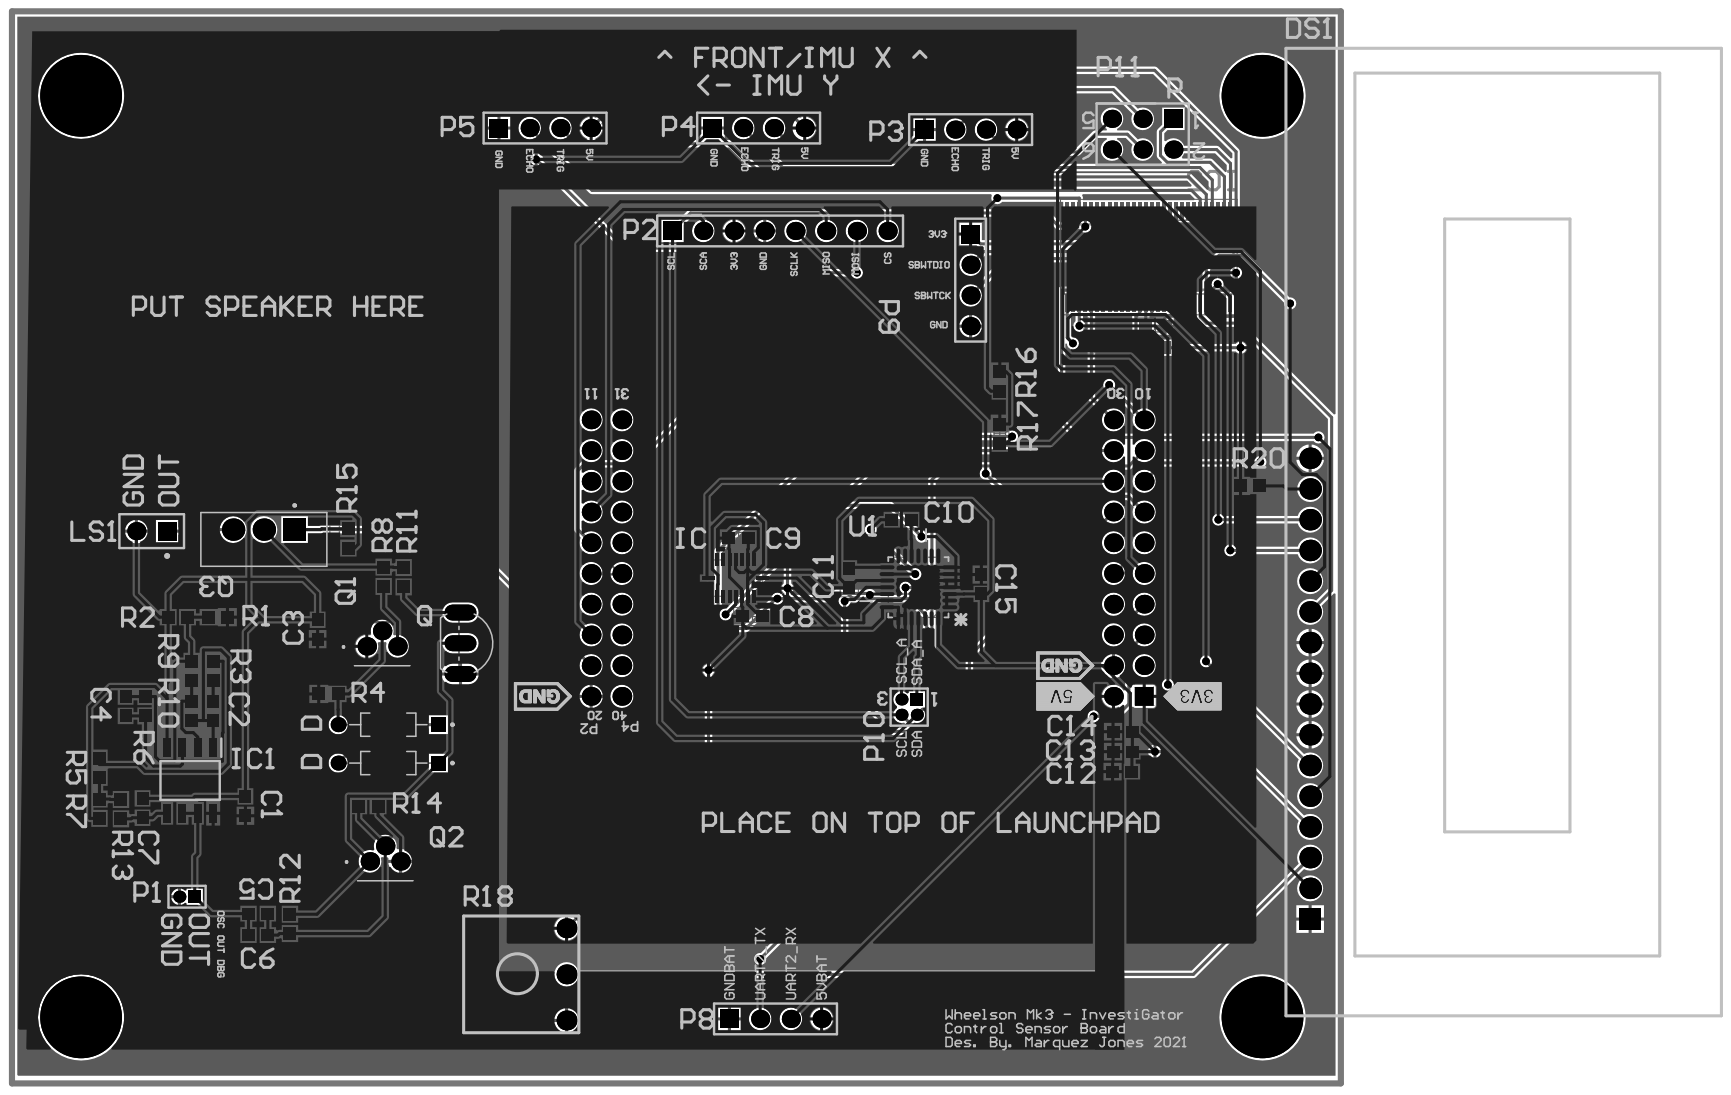
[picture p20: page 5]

Line# | Name | Description | Designator | Quantity | Manufacturer 1 | Manufacturer PartNumber 1 | Manufacturer Lifecycle1 | Supplier 1 | Supplier Part Number 1 | SupplierUnit Price1 | Supplier Subtotal 1
| Cap | | C1, C3 | 2 | Samsung | CL10B104KB8NNNC | VolumeProduction | Digi-Key | 1276-1000-1-ND
| Cap | | C2, C4 | 2 | Samsung | CL10B104KB8NNNC | VolumeProduction | Digi-Key | 1276-1000-1-ND
| Cap | | C5, C7, C13, C14 | 4 | Samsung | CL10B104KB8NNNC | VolumeProduction | Digi-Key | 1276-1000-1-ND
| Cap | | C6, C11 | 2 | Samsung | CL10B104KB8NNNC | VolumeProduction | Digi-Key | 1276-1000-1-ND
| Cap | | C8, C9, C15, C16 | 4 | Samsung | CL10B104KB8NNNC | VolumeProduction | Digi-Key | 1276-1000-1-ND
| Cap | | C10 | 1 | Samsung | CL10B104KB8NNNC | VolumeProduction | Digi-Key | 1276-1000-1-ND
| Cap | | C12 | 1 | Samsung | CL10B104KB8NNNC | VolumeProduction | Digi-Key | 1276-1000-1-ND
| 1N4148 | DIODEFAST SIGNAL 500MA/100V | D | 2
| LCD 44780 | | DS1 | 1
| BMI055 | Accelerometer,Gyroscope,6Axis SensorIC | | 1
| LM2904AVQDR | IntegratedCircuit | IC1 | 1
| MSP430FR4133IG56R | IntegratedCircuit | IC2 | 1
| Speaker | Loudspeaker | LS1 | 1
| MHDR1X2 | Header, 2-Pin | P1 | 1
| ArduCam | Header, 8-Pin | P2 | 1
| ULTRASONICHC-SR04 | Header, 4-Pin | P3, P4, P5 | 3
| SSQ-110-03-T-D | Receptacle,2.54mm,10x2,Tin,TH | P6 | 1 | Samtec | SSQ-110-03-T-D | VolumeProduction | Digi-Key | SAM1204-10-ND | 2.13 | 2.13
| SSQ-110-03-T-D | Receptacle,2.54mm,10x2,Tin,TH | P7 | 1 | Samtec | SSQ-110-03-T-D | VolumeProduction | Digi-Key | SAM1204-10-ND | 2.13 | 2.13
| Header 4 | Header, 4-Pin | P8, P9 | 2
| MHDR2X2 | Header, 2-Pin, Dual row | P10 | 1
| Header 3X2 | Header, 3-Pin, Dual row | P11 | 1
| 2N2907* | B i polar _BJT_Transistor PNP40V 600mAQ | | 1
| 2N2222A | TransistorBJTNPN | Q1,Q2 | 2
| IRF3205 | N-Channel 55V 110A(Tc) 200W(Tc) ThroQ3 | | 1
| Res | | R1, R2, R5, R15, R19 | 5 | StackpoleElectronRM CF0603JT10K0 | | VolumeProduction | Digi-Key | RMCF0603JT10K0CT-ND
| Res | | R3, R6 | 2 | StackpoleElectronRM CF0603JT10K0 | | VolumeProduction | Digi-Key | RMCF0603JT10K0CT-ND
| Res | | R4, R7, R12, R20 | 4 | StackpoleElectronRM CF0603JT10K0 | | VolumeProduction | Digi-Key | RMCF0603JT10K0CT-ND
| Res | | R8, R11, R13 | 3 | StackpoleElectronRM CF0603JT10K0 | | VolumeProduction | Digi-Key | RMCF0603JT10K0CT-ND
| Res | | R9 | 1 | StackpoleElectronRM CF0603JT10K0 | | VolumeProduction | Digi-Key | RMCF0603JT10K0CT-ND
| Res | | R10 | 1 | StackpoleElectronRM CF0603JT10K0 | | VolumeProduction | Digi-Key | RMCF0603JT10K0CT-ND
| Res | | R14 | 1 | StackpoleElectronRM CF0603JT10K0 | | VolumeProduction | Digi-Key | RMCF0603JT10K0CT-ND
| Res | | R16, R17 | 2 | StackpoleElectronRM CF0603JT10K0 | | VolumeProduction | Digi-Key | RMCF0603JT10K0CT-ND
| RPot_1 | Potentiometer | R18 | 1
| LSM303DLH | Accelerometer,Magnetometer,6Axis SenU1 | | 1



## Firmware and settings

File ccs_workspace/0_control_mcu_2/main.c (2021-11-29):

/*****************************************************************************
 * Name: main.c
 * Author: Marquez Jones
 * Desc: main program for MCU 2 on Control board
 *       for now will act as LCD driver
 *****************************************************************************/
#include "driverlib.h"
#include "ANY_LCD.h"
#include "Board.h"
#include <stdint.h>
#include <stdbool.h>
#include <stdio.h>

/********************************** defines *****************************/

#define CYCLES_TO_MS 1000 /* 1000 cyles = 1 ms */
#define CYCLES_TO_100US 100
#define US_TO_CM 0.034f
#define ULTRA_TIMEOUT 10 /* if longer than x ms before response timeout */
#define INT_MAX 2^(15)

#define ULTRA_PORT GPIO_PORT_P3 //all ultra sonics on same port
#define ULTRA_TRIG0 GPIO_PIN0 /* right */
#define ULTRA_ECHO0 GPIO_PIN1
#define ULTRA_TRIG1 GPIO_PIN2 /* center */
#define ULTRA_ECHO1 GPIO_PIN3
#define ULTRA_TRIG2 GPIO_PIN4 /* left */
#define ULTRA_ECHO2 GPIO_PIN5

#define UALERT_PIN GPIO_PIN4 /* pin o notify launchpad of ultrasonic warnings */
#define UALERT_PORT GPIO_PORT_P1

#define SLAVE_ADDRESS 0x48
#define RESET_LCD 0xFF /* special lcd code */

typedef enum ultra{
    ULTRA_0, /* right */
    ULTRA_1, /* center */
    ULTRA_2  /* left */
}ultra_t;

/********************************** prototypes *****************************/

/* inits */
void gpio_init(void);
void i2c_slave_init();

/* lcd functions */
void delayUS(uint32_t usec);
void lcdWrite(uint8_t bitfield);

/* ultra sonic */
void u_alert_high(void);
void u_alert_low(void);
int16_t check_ultra(ultra_t dev); /* returns the distance in cm of ultra sonic */
void trig_ultra(ultra_t dev);      /* trigger ultra */

/* return -1 on fail */
int8_t check_echo_ultra(ultra_t dev);/* read echo pin  */

/*
 * Name: i2c_data_handler
 * Desc: decodes i2c data
 *       for now will just handle the LCD
 */
void i2c_data_handler(uint8_t data);

/********************************** data ***********************************/

static const uint8_t reverse_nibble_lookup[8] = {
0x0, 0x8, 0x4, 0xc, 0x2, 0xa, 0x6, 0xe};
static uint8_t RXData;
static any_lcd_t lcd;

/* configured over i2c */
static int8_t too_close_cm = 30; /* 10 cm */

void main (void)
{
    //Stop WDT
    WDT_A_hold(WDT_A_BASE);

    gpio_init();

    i2c_slave_init();

    /****LCD INIT*****/
    lcd.delay_us  = &delayUS;
    lcd.lcd_write = &lcdWrite;

    LCD_Init(lcd); //will initialize lcd "logically" ie send the correct commands for 4 bit mode
    LCD_WriteString("ANY_LCD",lcd);

    /* leave this for now */
//    __bis_SR_register(CPUOFF + GIE);        // Enter LPM0 w/ interrupts
    __bis_SR_register(GIE);
//    __no_operation();
    while(1){

        int8_t dist_0 = check_ultra(ULTRA_0);
        int8_t dist_1 = check_ultra(ULTRA_1);
        int8_t dist_2 = check_ultra(ULTRA_2);

        if(dist_0 < too_close_cm){
            u_alert_high();
        }
        else if (dist_1 < too_close_cm){
            u_alert_high();
        }
        else if (dist_2 < too_close_cm){
            u_alert_high();
        }
        else{
            u_alert_low();
        }

    }
}

void u_alert_high(void){
    GPIO_setOutputHighOnPin(UALERT_PORT,UALERT_PIN);
}
void u_alert_low(void){
    GPIO_setOutputLowOnPin(UALERT_PORT,UALERT_PIN);
}

void gpio_init(void){
    /*
    #define ULTRA_PORT GPIO_PORT_P3 //all ultra sonics on same port
    #define ULTRA_TRIG0 GPIO_PIN0
    #define ULTRA_ECHO0 GPIO_PIN1
    #define ULTRA_TRIG1 GPIO_PIN2
    #define ULTRA_ECHO1 GPIO_PIN3
    #define ULTRA_TRIG2 GPIO_PIN4
    #define ULTRA_ECHO2 GPIO_PIN5
    */

    /* data pins on Port 7 */
    GPIO_setAsOutputPin(
        GPIO_PORT_P7,
        GPIO_PIN0 + GPIO_PIN1 + GPIO_PIN2 + GPIO_PIN3
    );

    /* control signal */
    GPIO_setAsOutputPin(
        GPIO_PORT_P1,
        GPIO_PIN0 + GPIO_PIN1 + GPIO_PIN2 + UALERT_PIN
    );

    /* i2c pins */
    GPIO_setAsPeripheralModuleFunctionInputPin(
        GPIO_PORT_P5,
        GPIO_PIN2 + GPIO_PIN3,
        GPIO_PRIMARY_MODULE_FUNCTION
    );

    /* ultra echo pins */
    GPIO_setAsInputPin(
        ULTRA_PORT,
        ULTRA_ECHO0 + ULTRA_ECHO1 + ULTRA_ECHO2
    );

    /* ultra trig pins */
    GPIO_setAsOutputPin(
        ULTRA_PORT,
        ULTRA_TRIG0 + ULTRA_TRIG1 + ULTRA_TRIG2
    );

  /*
   * Disable the GPIO power-on default high-impedance mode to activate
   * previously configured port settings
   */
    PMM_unlockLPM5();
}

void i2c_slave_init(){
    // eUSCI configuration
    EUSCI_B_I2C_initSlaveParam param = {0};
    param.slaveAddress = SLAVE_ADDRESS;
    param.slaveAddressOffset = EUSCI_B_I2C_OWN_ADDRESS_OFFSET0;
    param.slaveOwnAddressEnable = EUSCI_B_I2C_OWN_ADDRESS_ENABLE;
    EUSCI_B_I2C_initSlave(EUSCI_B0_BASE, &param);

    EUSCI_B_I2C_enable(EUSCI_B0_BASE);

    EUSCI_B_I2C_clearInterrupt(EUSCI_B0_BASE,
                EUSCI_B_I2C_RECEIVE_INTERRUPT0
                );

    EUSCI_B_I2C_enableInterrupt(EUSCI_B0_BASE,
                EUSCI_B_I2C_RECEIVE_INTERRUPT0
                );

}

/*
 * Name: i2c_data_handler
 * Desc: decodes i2c data
 *       for now will just handle the LCD
 */
void i2c_data_handler(uint8_t data){

    if(data == RESET_LCD){
        LCD_Reset(lcd);
    }
    else if(data == '\0'){
        /* do nothing */
    }
    else{
        /* char handling */
        LCD_WriteData(data,lcd);
    }

}

/*************************** ultra sonics ***************************/

/* returns the distance in cm of ultra sonic */
int16_t check_ultra(ultra_t dev){
    /* note: counts distance in increments of 100 us */

    trig_ultra(dev);

    /* wait to go high */
    int8_t res = GPIO_INPUT_PIN_LOW;
    uint32_t count = 0;
    while (res == GPIO_INPUT_PIN_LOW){
        res = check_echo_ultra(dev);
        __delay_cycles(CYCLES_TO_100US);
        if(count > 3*ULTRA_TIMEOUT){
            return 100; /*return huge number */
        }
        count++;
    }

    count = 0;
    while(res == GPIO_INPUT_PIN_HIGH){
        res = check_echo_ultra(dev);
        __delay_cycles(CYCLES_TO_100US);
        if(count > ULTRA_TIMEOUT){
            return 100; /* return huge number */
        }
        count++;
    }

    /* convert 100 us to distance in cm */
    float dist_cm = CYCLES_TO_100US * US_TO_CM * (float)count;
    return (int16_t)dist_cm;

}

/* trigger ultra */
/* return -1 on fail */
void trig_ultra(ultra_t dev){
    switch(dev){
    case ULTRA_0:
        GPIO_setOutputHighOnPin(ULTRA_PORT,ULTRA_TRIG0);
        __delay_cycles(10);
        GPIO_setOutputLowOnPin(ULTRA_PORT,ULTRA_TRIG0);
        break;
    case ULTRA_1:
        GPIO_setOutputHighOnPin(ULTRA_PORT,ULTRA_TRIG1);
        __delay_cycles(10);
        GPIO_setOutputLowOnPin(ULTRA_PORT,ULTRA_TRIG1);
        break;
    case ULTRA_2:
        GPIO_setOutputHighOnPin(ULTRA_PORT,ULTRA_TRIG2);
        __delay_cycles(10);
        GPIO_setOutputLowOnPin(ULTRA_PORT,ULTRA_TRIG2);
        break;
    default:
        break;
    }
}

/* read echo pin  */
int8_t check_echo_ultra(ultra_t dev){
    switch(dev){
    case ULTRA_0:
        return (int8_t)GPIO_getInputPinValue(ULTRA_PORT,ULTRA_ECHO0);
    case ULTRA_1:
        return (int8_t)GPIO_getInputPinValue(ULTRA_PORT,ULTRA_ECHO1);
    case ULTRA_2:
        return (int8_t)GPIO_getInputPinValue(ULTRA_PORT,ULTRA_ECHO2);
    default:
        return -1;
    }
}

/*************************** lcd code *******************************/

void delayUS(uint32_t usec){

    for(uint32_t i=0;i<usec;i++){
        __delay_cycles(1);
    }
}
void lcdWrite(uint8_t bitfield){
    /*
     * LCD DATA 7-4 -> P7.3 - P7.0
     * LCD E        -> P1.0
     * LCD RW       -> P1.1
     * LCD RS       -> P1.2
     */

    /* I needed to reverse the control nibble */
    uint8_t ctrl_bits = reverse_nibble_lookup[bitfield&0x07] >> 1;

    /* P1 control signals */
    GPIO_setOutputLowOnPin(GPIO_PORT_P1, ( ~ctrl_bits ) & 0x07);
    GPIO_setOutputHighOnPin(GPIO_PORT_P1, ctrl_bits & 0x07);

    /* P7 data signals */
    GPIO_setOutputLowOnPin(GPIO_PORT_P7, (~bitfield >> 4) & 0x0F );
    GPIO_setOutputHighOnPin(GPIO_PORT_P7, (bitfield >> 4) & 0x0F );
}

/***************************** INTERRUPTS ********************************/

#if defined(__TI_COMPILER_VERSION__) || defined(__IAR_SYSTEMS_ICC__)
#pragma vector=USCI_B0_VECTOR
__interrupt
#elif defined(__GNUC__)
__attribute__((interrupt(USCI_B0_VECTOR)))
#endif
void USCIB0_ISR(void)
{
    switch(__even_in_range(UCB0IV, USCI_I2C_UCBIT9IFG))
    {
        case USCI_NONE:             // No interrupts break;
            break;
        case USCI_I2C_UCALIFG:      // Arbitration lost
            break;
        case USCI_I2C_UCNACKIFG:    // NAK received (master only)
            break;
        case USCI_I2C_UCSTTIFG:     // START condition detected with own address (slave mode only)
            break;
        case USCI_I2C_UCSTPIFG:     // STOP condition detected (master & slave mode)
            break;
        case USCI_I2C_UCRXIFG3:     // RXIFG3
            break;
        case USCI_I2C_UCTXIFG3:     // TXIFG3
            break;
        case USCI_I2C_UCRXIFG2:     // RXIFG2
            break;
        case USCI_I2C_UCTXIFG2:     // TXIFG2
            break;
        case USCI_I2C_UCRXIFG1:     // RXIFG1
            break;
        case USCI_I2C_UCTXIFG1:     // TXIFG1
            break;
        case USCI_I2C_UCRXIFG0:     // RXIFG0
            RXData = EUSCI_B_I2C_slaveGetData(EUSCI_B0_BASE);
            i2c_data_handler(RXData);
            break;
        case USCI_I2C_UCTXIFG0:     // TXIFG0
            break;
        case USCI_I2C_UCBCNTIFG:    // Byte count limit reached (UCBxTBCNT)
            break;
        case USCI_I2C_UCCLTOIFG:    // Clock low timeout - clock held low too long
            break;
        case USCI_I2C_UCBIT9IFG:    // Generated on 9th bit of a transmit (for debugging)
            break;
        default:
            break;
    }
}

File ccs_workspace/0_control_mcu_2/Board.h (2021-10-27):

/* --COPYRIGHT--,BSD
 * Copyright (c) 2017, Texas Instruments Incorporated
 * All rights reserved.
 *
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
 * *  Redistributions of source code must retain the above copyright
 *    notice, this list of conditions and the following disclaimer.
 *
 * *  Redistributions in binary form must reproduce the above copyright
 *    notice, this list of conditions and the following disclaimer in the
 *    documentation and/or other materials provided with the distribution.
 *
 * *  Neither the name of Texas Instruments Incorporated nor the names of
 *    its contributors may be used to endorse or promote products derived
 *    from this software without specific prior written permission.
 *
 * THIS SOFTWARE IS PROVIDED BY THE COPYRIGHT HOLDERS AND CONTRIBUTORS "AS IS"
 * AND ANY EXPRESS OR IMPLIED WARRANTIES, INCLUDING, BUT NOT LIMITED TO,
 * THE IMPLIED WARRANTIES OF MERCHANTABILITY AND FITNESS FOR A PARTICULAR
 * PURPOSE ARE DISCLAIMED. IN NO EVENT SHALL THE COPYRIGHT OWNER OR
 * CONTRIBUTORS BE LIABLE FOR ANY DIRECT, INDIRECT, INCIDENTAL, SPECIAL,
 * EXEMPLARY, OR CONSEQUENTIAL DAMAGES (INCLUDING, BUT NOT LIMITED TO,
 * PROCUREMENT OF SUBSTITUTE GOODS OR SERVICES; LOSS OF USE, DATA, OR PROFITS;
 * OR BUSINESS INTERRUPTION) HOWEVER CAUSED AND ON ANY THEORY OF LIABILITY,
 * WHETHER IN CONTRACT, STRICT LIABILITY, OR TORT (INCLUDING NEGLIGENCE OR
 * OTHERWISE) ARISING IN ANY WAY OUT OF THE USE OF THIS SOFTWARE,
 * EVEN IF ADVISED OF THE POSSIBILITY OF SUCH DAMAGE.
 * --/COPYRIGHT--*/
/**
 * ===
 * Board.h
 * ===
 * This file is meant to provide generic GPIO selection definitions that allows
 * DriverLib to be used portably across different LaunchPads. The same module
 * pin might not be populated on the same physical port and pin on different
 * LaunchPads.
 *
 * This file is intended to be modified and updated by individual users based
 * on application need. It will be initially populated according to common
 * peripherals available on a LaunchPad board, but by all means not complete.
 *
 * GPIO_PRIMARY_MODULE_FUNCTION indicates Port SEL bits are 01
 * GPIO_SECONDARY_MODULE_FUNCTION indicates Port SEL bits are 10
 * GPIO_TERNARY_MODULE_FUNCTION indicates Port SEL bits are 11
 * If the Port SEL bits are 00, the FUNCTION bits should be ignored
 * Please consult device datasheet for more info, under "Input/Output Diagrams"
 *
 **/

#ifndef __BOARD_H__
#define __BOARD_H__

#ifdef __MSP430FR4133__

#define GPIO_PORT_LED1          GPIO_PORT_P1
#define GPIO_PIN_LED1           GPIO_PIN0
#define GPIO_PORT_LED2          GPIO_PORT_P4
#define GPIO_PIN_LED2           GPIO_PIN0
#define GPIO_PORT_S1            GPIO_PORT_P1
#define GPIO_PIN_S1             GPIO_PIN2

#define GPIO_PORT_ADC7          GPIO_PORT_P1
#define GPIO_PIN_ADC7           GPIO_PIN7
#define GPIO_FUNCTION_ADC7      GPIO_PRIMARY_MODULE_FUNCTION

#define GPIO_PORT_MCLK          GPIO_PORT_P1
#define GPIO_PIN_MCLK           GPIO_PIN4
#define GPIO_FUNCTION_MCLK      GPIO_PRIMARY_MODULE_FUNCTION
#define GPIO_PORT_SMCLK         GPIO_PORT_P8
#define GPIO_PIN_SMCLK          GPIO_PIN0
#define GPIO_FUNCTION_SMCLK     GPIO_PRIMARY_MODULE_FUNCTION
#define GPIO_PORT_ACLK          GPIO_PORT_P8
#define GPIO_PIN_ACLK           GPIO_PIN1
#define GPIO_FUNCTION_ACLK      GPIO_PRIMARY_MODULE_FUNCTION

#define GPIO_PORT_UCA0TXD       GPIO_PORT_P1
#define GPIO_PIN_UCA0TXD        GPIO_PIN0
#define GPIO_FUNCTION_UCA0TXD   GPIO_PRIMARY_MODULE_FUNCTION
#define GPIO_PORT_UCA0RXD       GPIO_PORT_P1
#define GPIO_PIN_UCA0RXD        GPIO_PIN1
#define GPIO_FUNCTION_UCA0RXD   GPIO_PRIMARY_MODULE_FUNCTION

#define GPIO_PORT_UCB0SCL       GPIO_PORT_P5
#define GPIO_PIN_UCB0SCL        GPIO_PIN3
#define GPIO_FUNCTION_UCB0SCL   GPIO_PRIMARY_MODULE_FUNCTION
#define GPIO_PORT_UCB0SDA       GPIO_PORT_P5
#define GPIO_PIN_UCB0SDA        GPIO_PIN2
#define GPIO_FUNCTION_UCB0SDA   GPIO_PRIMARY_MODULE_FUNCTION

#endif // __MSP430FR4133__

#ifdef __MSP430FR2311__

#define GPIO_PORT_LED1          GPIO_PORT_P1
#define GPIO_PIN_LED1           GPIO_PIN0
#define GPIO_PORT_LED2          GPIO_PORT_P2
#define GPIO_PIN_LED2           GPIO_PIN0
#define GPIO_PORT_S1            GPIO_PORT_P1
#define GPIO_PIN_S1             GPIO_PIN1

#define GPIO_PORT_ADC7          GPIO_PORT_P1
#define GPIO_PIN_ADC7           GPIO_PIN7
#define GPIO_FUNCTION_ADC7      GPIO_PRIMARY_MODULE_FUNCTION

#define GPIO_PORT_MCLK          GPIO_PORT_P2
#define GPIO_PIN_MCLK           GPIO_PIN6
#define GPIO_FUNCTION_MCLK      GPIO_PRIMARY_MODULE_FUNCTION
#define GPIO_PORT_SMCLK         GPIO_PORT_P1
#define GPIO_PIN_SMCLK          GPIO_PIN0
#define GPIO_FUNCTION_SMCLK     GPIO_SECONDARY_MODULE_FUNCTION
#define GPIO_PORT_ACLK          GPIO_PORT_P1
#define GPIO_PIN_ACLK           GPIO_PIN1
#define GPIO_FUNCTION_ACLK      GPIO_SECONDARY_MODULE_FUNCTION
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

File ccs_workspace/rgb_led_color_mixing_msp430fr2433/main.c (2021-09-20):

/* --COPYRIGHT--,BSD
 * Copyright (c) 2020, Texas Instruments Incorporated
 * All rights reserved.
 *
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
 * *  Redistributions of source code must retain the above copyright
 *    notice, this list of conditions and the following disclaimer.
 *
 * *  Redistributions in binary form must reproduce the above copyright
 *    notice, this list of conditions and the following disclaimer in the
 *    documentation and/or other materials provided with the distribution.
 *
 * *  Neither the name of Texas Instruments Incorporated nor the names of
 *    its contributors may be used to endorse or promote products derived
 *    from this software without specific prior written permission.
 *
 * THIS SOFTWARE IS PROVIDED BY THE COPYRIGHT HOLDERS AND CONTRIBUTORS "AS IS"
 * AND ANY EXPRESS OR IMPLIED WARRANTIES, INCLUDING, BUT NOT LIMITED TO,
 * THE IMPLIED WARRANTIES OF MERCHANTABILITY AND FITNESS FOR A PARTICULAR
 * PURPOSE ARE DISCLAIMED. IN NO EVENT SHALL THE COPYRIGHT OWNER OR
 * CONTRIBUTORS BE LIABLE FOR ANY DIRECT, INDIRECT, INCIDENTAL, SPECIAL,
 * EXEMPLARY, OR CONSEQUENTIAL DAMAGES (INCLUDING, BUT NOT LIMITED TO,
 * PROCUREMENT OF SUBSTITUTE GOODS OR SERVICES; LOSS OF USE, DATA, OR PROFITS;
 * OR BUSINESS INTERRUPTION) HOWEVER CAUSED AND ON ANY THEORY OF LIABILITY,
 * WHETHER IN CONTRACT, STRICT LIABILITY, OR TORT (INCLUDING NEGLIGENCE OR
 * OTHERWISE) ARISING IN ANY WAY OUT OF THE USE OF THIS SOFTWARE,
 * EVEN IF ADVISED OF THE POSSIBILITY OF SUCH DAMAGE.
 * --/COPYRIGHT--*/
//******************************************************************************
//  MSP430FR2433 Demo - UART RGB LED Color Mixing
//
//  Description: This example sets up Timer A to output PWM waveforms with
//  variable duty cycles based on UART byte values. These PWM waveforms control
//  the color of an external RGB LED. The PWM values are updated after every 3rd
//  byte received via UART.
//  ACLK = default REFO ~32768Hz
//  SMCLK = MCLK = DCO + FLL + 32KHz REFO REF = 1MHz
//
//           MSP430FR2433
//         ---------------
//     /|\|               |
//      | |               |
//      --|RST            |
//        |          P2.5 |<--- UART RX
//        |               |
//        |          P2.6 |---> UART TX
//        |               |
//        |          P1.2 |---> TA0.2 (Red)
//        |          P1.5 |---> TA1.1 (Green)
//        |          P1.4 |---> TA1.2 (Blue)
//
//   Aaron Barrera
//   Texas Instruments Inc.
//   October 2020
//   Built with Code Composer Studio v9.2 and IAR 7.20
//******************************************************************************

#include <msp430.h>
#include <stdint.h>
#include <stdbool.h>

unsigned int valueIntoCCR(unsigned char colorVal);
#define GPIO_ALL        BIT0|BIT1|BIT2|BIT3|BIT4|BIT5|BIT6|BIT7
#define MCLK_FREQ_MHZ 1                                          // MCLK = 1MHz

// Declare global variables
volatile uint8_t uartByteNum;                                    // 0 for high, 1 for low

 // These variables are initialized in callbacks.h, so must be global here to use for UART
 volatile uint8_t redVal;       //Value of red
 volatile uint8_t greenVal;     //Value of green
 volatile uint8_t blueVal;      //Value of blue

// main.c
int main(void)
{
    WDTCTL = WDTPW | WDTHOLD;                                     // Stop watchdog timer

    __bis_SR_register(SCG0);                                      // disable FLL

    // Initialize Clock System
    // SMCLK = MCLK = DCO + FLL + 32KHz REFO REF = 1MHz
    CSCTL3 |= SELREF__REFOCLK;                                    // Set REFO as FLL reference source
    CSCTL1 = DCOFTRIMEN | DCOFTRIM0 | DCOFTRIM1 | DCORSEL_0;      // DCOFTRIM=3, DCO Range = 1MHz
    CSCTL2 = FLLD_0 + 30;                                         // DCODIV = 1MHz
    __delay_cycles(3);
    __bic_SR_register(SCG0);                                      // enable FLL

    CSCTL4 = SELMS__DCOCLKDIV | SELA__REFOCLK;                    // set default REFO(~32768Hz) as ACLK source, ACLK = 32768Hz
                                                                  // default DCODIV as MCLK and SMCLK source
    // Initialize globals
    uartByteNum = 0;
    redVal = 0;
    greenVal = 0;
    blueVal = 0;

    //RED = P1.2 = TA0.2
    //GREEN = P1.4 = TA1.2
    //BLUE = P1.5 = TA1.1

    // Initialize ports
    P1OUT = 0;                                                    // Set all pins low
    P1DIR = GPIO_ALL;

    P1SEL1 |= BIT2 | BIT4 | BIT5;                                 // P1.1, P1.2, P1.5 options select

    P2OUT = 0;                                                    // Set all pins low
    P2DIR = GPIO_ALL;                                             // Set all pins as outputs

    P3OUT = 0;                                                    // Set all pins low
    P3DIR = GPIO_ALL;                                             // Set all pins as outputs

    P2SEL0 |= BIT5 | BIT6;                                        // Configure P1.4 and P1.5 for UART
    // Disable the GPIO power-on default high-impedance
    // mode to activate previously configured port settings
    PM5CTL0 &= ~LOCKLPM5;

    // Configure UART 9600 baud
    UCA1CTLW0 |= UCSWRST;                                         // eUSCI_A logic held in reset state.
    UCA1CTLW0 |= UCSSEL__SMCLK;                                   // One stop bit, no parity, LSB first, 8-bit data as the default setting
    UCA1BR0 = 6;                                                  // 1000000/16/9600
    UCA1BR1 = 0x00;
    UCA1MCTLW = 0x2000 | UCOS16 | UCBRF_8;
    UCA1CTLW0 &= ~UCSWRST;                                        // eUSCI_A reset released for operation
    UCA1IE = UCRXIE;                                              // Enable USCI_A0 RX interrupt

    // Initialize Timer_A
    TA0CCR0 = 1000-1;                       // PWM Period for TA0
    TA0CCTL2 = OUTMOD_7;                    // CCR2 reset/set
    TA0CCR2 = 0;                            // CCR2 PWM duty cycle (RED)

    TA1CCR0 = 1000-1;                       // PWM Period for TA1
    TA1CCTL2 = OUTMOD_7;                    // CCR1 reset/set
    TA1CCR2 = 0;                            // CCR1 PWM duty cycle (GREEN)
    TA1CCTL1 = OUTMOD_7;                    // CCR2 reset/set
    TA1CCR1 = 0;                            // CCR2 PWM duty cycle (BLUE)

    TA0CTL = TASSEL__SMCLK | MC__UP | TACLR;  // SMCLK, up mode, clear TA0R
    TA1CTL = TASSEL__SMCLK | MC__UP | TACLR;  // SMCLK, up mode, clear TA1R

    __bis_SR_register(LPM0_bits | GIE);                       // Go to LPM0 with interrupts
    __no_operation();
}
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

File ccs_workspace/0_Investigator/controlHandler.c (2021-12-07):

/*
 * Name: controlHandler.c
 * Desc: has multiple tasks
 *       1) must send updates to client about status updates ie when finishes moving
 *       2) must receive commands and act on them
 *       3) send uart messages to motor board
 *       4)
 */

#include <stdbool.h>
#include <stdint.h>
#include <stdlib.h>
#include <stddef.h>
#include <stdio.h>
#include <string.h>

/* POSIX Header files */
#include <pthread.h>
#include <semaphore.h>
#include <unistd.h>

/* Driver Header files */
#include <ti/drivers/GPIO.h>
#include <ti/drivers/I2C.h>
#include <ti/drivers/SPI.h>
#include <ti/display/Display.h>
#include <ti/sysbios/knl/Clock.h>
#include <ti/sysbios/knl/Task.h>

#include "shared.h"
#include "board.h"
#include "sensor_drivers/LSM303DLH.h"

extern Display_Handle display;

typedef uint8_t motor_cmd_t;
const motor_cmd_t MOTOR_TURN_RIGHT = 'R';
const motor_cmd_t MOTOR_TURN_LEFT  = 'L';
const motor_cmd_t MOVE_FORW  = 'F';
const motor_cmd_t MOVE_RVRS  = 'B';
const motor_cmd_t MOTOR_STOP = 'S';

typedef enum state{
    ST_WAIT_CMD, /* wait for command via pipe */
    ST_EXE_CMD,  /* execution state ; will send updates here */
    ST_COL,      /* collision handling ; will send updates here */
    ST_RESET,    /* robot reset operation */
}state_t;


/**************************** STATE HANDLER *************************/

/* wait handler */
static void wait_handler(state_t *next);

/* exe handler */
static void exe_handler(state_t *next);

/* collision handler */
static void col_handler(state_t *next);

/* reset handler */
static void reset_handler(state_t *next);

/* reroute handler */
static void reroute_handler(state_t *next);

/**************************** MSG FUNCTIONS *************************/

/* tell client current pos */
static void send_new_pos(void);

/* tell client robot is blocked */
static void send_blocked_msg(void);

/* send some kind of message to the client */
static void send_msg(char *msg);

static void send_heading(void);

/**************************** MOVE ROBOT *************************/

/* send command to motor board */
static int send_motor_cmd(motor_cmd_t cmd);

/* rotate to heading */
/* makes robot rotate to new heading by sending motor commands*/
static int rotate_to_heading(float new_heading);

/* figure out heading in order to find next coord */
static float calc_heading(uint8_t new_x, uint8_t new_y);

/*
 * figure out next coord
 * basic pathing algo, go to the next closest grid location
 * will move with new york style coords, no diagonal movements
 */
static int calc_next_coord(uint8_t new_x,
                            uint8_t new_y,
                            uint8_t *next_x,
                            uint8_t *next_y);

/**************************** FAKE HEADING *************************/

/*
 * Fake heading code is for dead reckoning system
 * magnetometer was bad so robot just assumes direction
 * based on number of times it has told motor board to rotate
 * from "north"
 */

float fake_heading;

/*
 *
 */
float get_fake_heading();

/*
 *
 */
void update_fake_heading(float heading);

/**************************** GLOBAL VARIABLES *************************/

static pdu_t rx_pdu;
static pdu_t tx_pdu;

bool blocked_flag = false;


void controlThread(void *arg0){

    fake_heading = HEAD_N;
    lcd_reset();
    state_t state = ST_WAIT_CMD;
    pdu_cmd_t cmd = PDU_STOP;

    while(1){

        Display_printf(display,0,0,"NEW COMMAND");
        if(blocked_flag == true){
            state = ST_COL;
        }
        switch(state){
        case ST_WAIT_CMD:
            lcd_reset();
            lcd_string("WAIT STATE");
            wait_handler(&state);

            break;
        case ST_EXE_CMD:
            lcd_reset();
            lcd_string("EXE STATE");
            exe_handler(&state);
            break;

        case ST_REROUTE:
            lcd_reset();
            lcd_string("REROUTE STATE");
            reroute_handler(&state);
            break;

        case ST_COL:
            lcd_reset();
            lcd_string("COLLIDE STATE");
            col_handler(&state);
            break;

        case ST_RESET:
            reset_handler(&state);
            break;

        default:
            state = ST_WAIT_CMD;
            break;
        }
    }
}

void safetyHandler(uint_least8_t index){

    bool val = read_u_alert();
    if(val){
        Display_printf(display,0,0,"U_ALERT: HIGH");
        send_motor_cmd(MOTOR_STOP);
        blocked_flag = true;
        turn_on_speaker();
    }
    else{
        Display_printf(display,0,0,"U_ALERT: LOW");
        blocked_flag = false;
        turn_off_speaker();
    }

    return;
}

/* wait handler */
static void wait_handler(state_t *next){

    /* stop motor when in this state */
    send_motor_cmd(MOTOR_STOP);

    pdu_fifo_get(&rx_pdu_fifo_g,&rx_pdu);
//    pdu_fifo_put(&tx_pdu_fifo_g,&rx_pdu);

    switch (rx_pdu.cmd){
    case PDU_MOVE:
//        Display_printf(display, 0, 0,"MOVE CMD");
        *next = ST_EXE_CMD;
        break;
    case PDU_RESET:
        *next = ST_RESET;
        break;

    /* direct control */
    case PDU_GO_FORWARD:
        send_motor_cmd(MOVE_FORW);
        *next = ST_WAIT_CMD;
        break;
    case PDU_GO_REV:
        send_motor_cmd(MOVE_RVRS);
        *next = ST_WAIT_CMD;
        break;
    case PDU_TURN_LEFT:
        send_motor_cmd(MOTOR_TURN_LEFT);
        *next = ST_WAIT_CMD;
        break;
    case PDU_TURN_RIGHT:
        send_motor_cmd(MOTOR_TURN_RIGHT);
        *next = ST_WAIT_CMD;
        break;
    case PDU_STOP:
        send_motor_cmd(MOTOR_STOP);
        *next = ST_WAIT_CMD;
        break;
    default:
        Display_printf(display, 0, 0, "Garbage");
        break;
    }

    send_new_pos();

}

/* reroute handler */
static void reroute_handler(state_t *next){


}

/* exe handler */
static void exe_handler(state_t *next){
    /*
     * note , robot will only move in either x or y direction
     * at a time
     */

    /* parse pdu data to figure out what to do */
    bool done = false;

    uint8_t new_x = rx_pdu.x; /* dest */
    uint8_t new_y = rx_pdu.y;

    uint8_t next_x;
    uint8_t next_y;

    float new_heading;

    do{
        if(blocked_flag){
//            send_blocked_msg();
//            send_msg("FAILED: TRY REROUTE");

            *next = ST_COL;
            return;
        }
        if(rx_pdu.cmd == PDU_MOVE){
            uint8_t curr_x;
            uint8_t curr_y;

            get_position(&curr_x, &curr_y);

//            Display_printf(display, 0, 0,"E X E \n");


            /* we've reached the correct location */
            if(curr_x == new_x && curr_y == new_y){
                done = true; /* done with moving */
            }

//            /* get next coord */
            calc_next_coord(new_x,new_y,&next_x,&next_y);

            /* get heading based on coord */
            new_heading = calc_heading(new_x,new_y);

            /* rotate robot to heading */
            rotate_to_heading(new_heading);
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

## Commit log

2021-09-20 big update
    [BIOS.obj, CC3220SF_BOM.xls, CC3220S_BOM.xls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]
2021-09-21 control board updates
    [MCU065E1_Host_Interface.SchDoc, analog.SchDoc, mcu_main.SchDoc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]
2021-09-24 board layout started; still need to verfiy schematic items
    [BIOS.obj, Control_Board.PrjPcb, analog.SchDoc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]
2021-09-28 updating board with msp430 schematic
    [Control_Board.PrjPcb, analog.SchDoc, mcu_main.PcbDoc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]
2021-10-04 made project with both camera and tcp - new baseline
    [Control_Board.PrjPcb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]
2021-10-08 OwO, a jpeg in the mail
    [mutex.cfg]
2021-10-09 good progress on camera client and server (embedded)
2021-10-27 several firmware updates for mcu2 and launchpad
    [msp430.SchDoc, sensors.SchDoc]
2021-10-27 Added Code Examples and Started Motor Firmware
2021-10-30 msp430 firmware finished, updates to cc3235
    [msp430.SchDoc]
2021-11-19 Pushing Motorboard Resources
    Includes altium files and code updates
    [Alarm.SchDoc, BuckConverter.SchDoc, HBridge.SchDoc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]
2021-11-22 Preliminary Respin
    Uploaded Altium files for respun board
    [Alarm.SchDoc, BuckConverter.SchDoc, HBridge.SchDoc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]
2021-11-22 Uploaded Board Respin for Sanity check
    Pls work next week if not oh well
    [Alarm.SchDoc, BuckConverter.SchDoc, HBridge.SchDoc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]
2021-11-27 changed reverse to B in control board code
    [PCB1.PcbDoc]
2021-11-27 System Integration, Motorboard V1 Code
    It should work lmao KEKW pls
2021-11-29 Lower Software Delay
    Update to current running software 11/29
2021-11-29 swapped to dead reckoning
    [controlHandler.c, main.c]
2021-12-03 Motorboard stop flag implemented
    should not miss any commands anymore
